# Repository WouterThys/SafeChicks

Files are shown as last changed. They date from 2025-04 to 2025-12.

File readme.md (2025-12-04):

# Safe Chicks

Chicks need to be safe so make door go brrrr.

## Ideas/Notes
 - Chord attacked to door and motor winds up/down to open/close door
 - Light sensor 
 - Limit switch -> use the iCab galenus switches? -> magnetic so will not weir out I guess
 - Solar powered?
 - Controller? What I have is:
    - Pico Pi
    - Arduino
    - Raspberry pi 3
    - Beaglebone black
    - Adafruit Huzzah -> has ESP.. 
 - Camera to see if checks are there -> would need raspberry for that (arduino is too lightweight)
 - DC motor
      https://www.farnell.com/datasheets/4376711.pdf?_gl=1*1atfsg3*_gcl_au*MjAyNTY1MDc1NS4xNzQxNjI0NTgy

## Used in V2

### Mouser
426-DRI0044
Fabrik. Artikelnum.: DRI0044
DFRobot 2x1.2A DC Motor Driv / Stroombeheer IC Ontwikkelinghulpmiddelen
TARIC:8473302000 ECCN:EAR99 COO:CN

426-FIT0489-D
Fabrik. Artikelnum.: FIT0489-D
DFRobot Turbo Metal Gear Wor / DFRobo-accessoires
TARIC:8471500090 ECCN:EAR99 COO:CN

653-D2HW-C223MR
Fabrik. Artikelnum.: D2HW-C223MR
Omron Electronics Subminiature Basic S / Basis- / klikschakelaars
TARIC:8536508099 ECCN:EAR99 COO:IT

### RobotShop
RB-Jsu-84 37mm Motor Mount For Titan Series (Pair) 5-4-G 1 1 0 €5.71 €5.71
RB-Sct-941 15T Timing Pinion Pulley (6mm) 02-6-B 1 1 0 €9.45 €9.45
RB-Phi-457 Waterproof Enclosure 200x120x75 w/ Transparent Lid M05-2-D 1 1 0 €13.12 €13.12

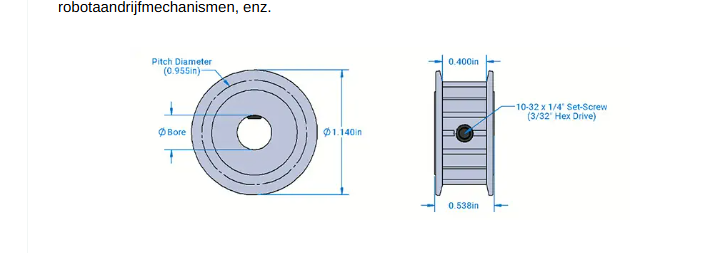
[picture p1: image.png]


## Usefull links
DIY chicken door:
https://davenaves.com/blog/interests-projects/chickens/chicken-coop/arduino-chicken-door/#

Battery management system
https://www.dfrobot.com/product-1714.html

Arduino low power
https://docs.arduino.cc/learn/electronics/low-power/

## Measurements

### POC Arduino Uno (17/03 16:20)
  - added 4[Ohm] resistor between 12V supply
  - Idle ~140mV => 4,9 mW
  - Run  ~1,30V => 423 mW

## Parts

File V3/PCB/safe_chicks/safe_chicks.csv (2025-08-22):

Reference | Value | Footprint | Datasheet | Qty | DNP | Exclude from BOM | Exclude from Board
C1,C2,C4,C10 | 100n | Capacitor_SMD:C_0603_1608Metric_Pad1.08x0.95mm_HandSolder | ~ | 4
C3 | 1u | Capacitor_Tantalum_SMD:CP_EIA-3216-10_Kemet-I_HandSolder | ~ | 1
C5 | 10u | Capacitor_Tantalum_SMD:CP_EIA-3216-10_Kemet-I_HandSolder | ~ | 1
C6,C7 | 10n | Capacitor_SMD:C_0603_1608Metric_Pad1.08x0.95mm_HandSolder | ~ | 2
C8,C9,C11,C12 | 1u | Capacitor_SMD:C_0603_1608Metric_Pad1.08x0.95mm_HandSolder | ~ | 4
D1 | 1007 | Diode_THT:D_DO-15_P10.16mm_Horizontal | ~ | 1
D2,D3,D4,D5,D6,D7 | LED_Small | LED_SMD:LED_0603_1608Metric_Pad1.05x0.95mm_HandSolder | ~ | 6
H1,H2,H3,H4 | MountingHole | MountingHole:MountingHole_3.2mm_M3_Pad_Via | ~ | 4 |  | Excluded from BOM
J1 | 5V | TerminalBlock:TerminalBlock_bornier-2_P5.08mm | ~ | 1
J2 | PGM | Connector_PinHeader_2.54mm:PinHeader_1x06_P2.54mm_Vertical | ~ | 1
J3 | Serial | Connector_Molex:Molex_PicoBlade_53047-0410_1x04_P1.25mm_Vertical | ~ | 1
J4 | Buttons | Connector_Molex:Molex_PicoBlade_53047-0410_1x04_P1.25mm_Vertical | ~ | 1
J5 | MTR | Connector_PinHeader_2.54mm:PinHeader_1x06_P2.54mm_Vertical | ~ | 1
J6 | Sensors | Connector_Molex:Molex_PicoBlade_53047-0410_1x04_P1.25mm_Vertical | ~ | 1
J8 | Switches | Connector_Molex:Molex_PicoBlade_53047-0410_1x04_P1.25mm_Vertical | ~ | 1
J9 | LED-Enable | Connector_PinHeader_2.54mm:PinHeader_1x03_P2.54mm_Vertical | ~ | 1
R1,R10,R11,R18,R20 | 10k | Resistor_SMD:R_0603_1608Metric_Pad0.98x0.95mm_HandSolder | ~ | 5
R2,R3 | 613k | Resistor_SMD:R_0603_1608Metric_Pad0.98x0.95mm_HandSolder | ~ | 2
R4 | 332k | Resistor_SMD:R_0603_1608Metric_Pad0.98x0.95mm_HandSolder | ~ | 1
R6,R7,R17,R19 | 100k | Resistor_SMD:R_0603_1608Metric_Pad0.98x0.95mm_HandSolder | ~ | 4
R8,R9,R12,R13,R14,R15 | 1k | Resistor_SMD:R_0603_1608Metric_Pad0.98x0.95mm_HandSolder | ~ | 6
R16 | 47k | Resistor_SMD:R_0603_1608Metric_Pad0.98x0.95mm_HandSolder | ~ | 1
SW1 | Reset | Button_Switch_THT:SW_PUSH_6mm_H4.3mm | ~ | 1
U1 | PIC18F2550-ISP | Package_DIP:DIP-28_W7.62mm | http://ww1.microchip.com/downloads/en/devicedoc/39632c.pdf | 1
Y1 | 16MHz | Crystal:Crystal_HC49-U_Vertical | ~ | 1

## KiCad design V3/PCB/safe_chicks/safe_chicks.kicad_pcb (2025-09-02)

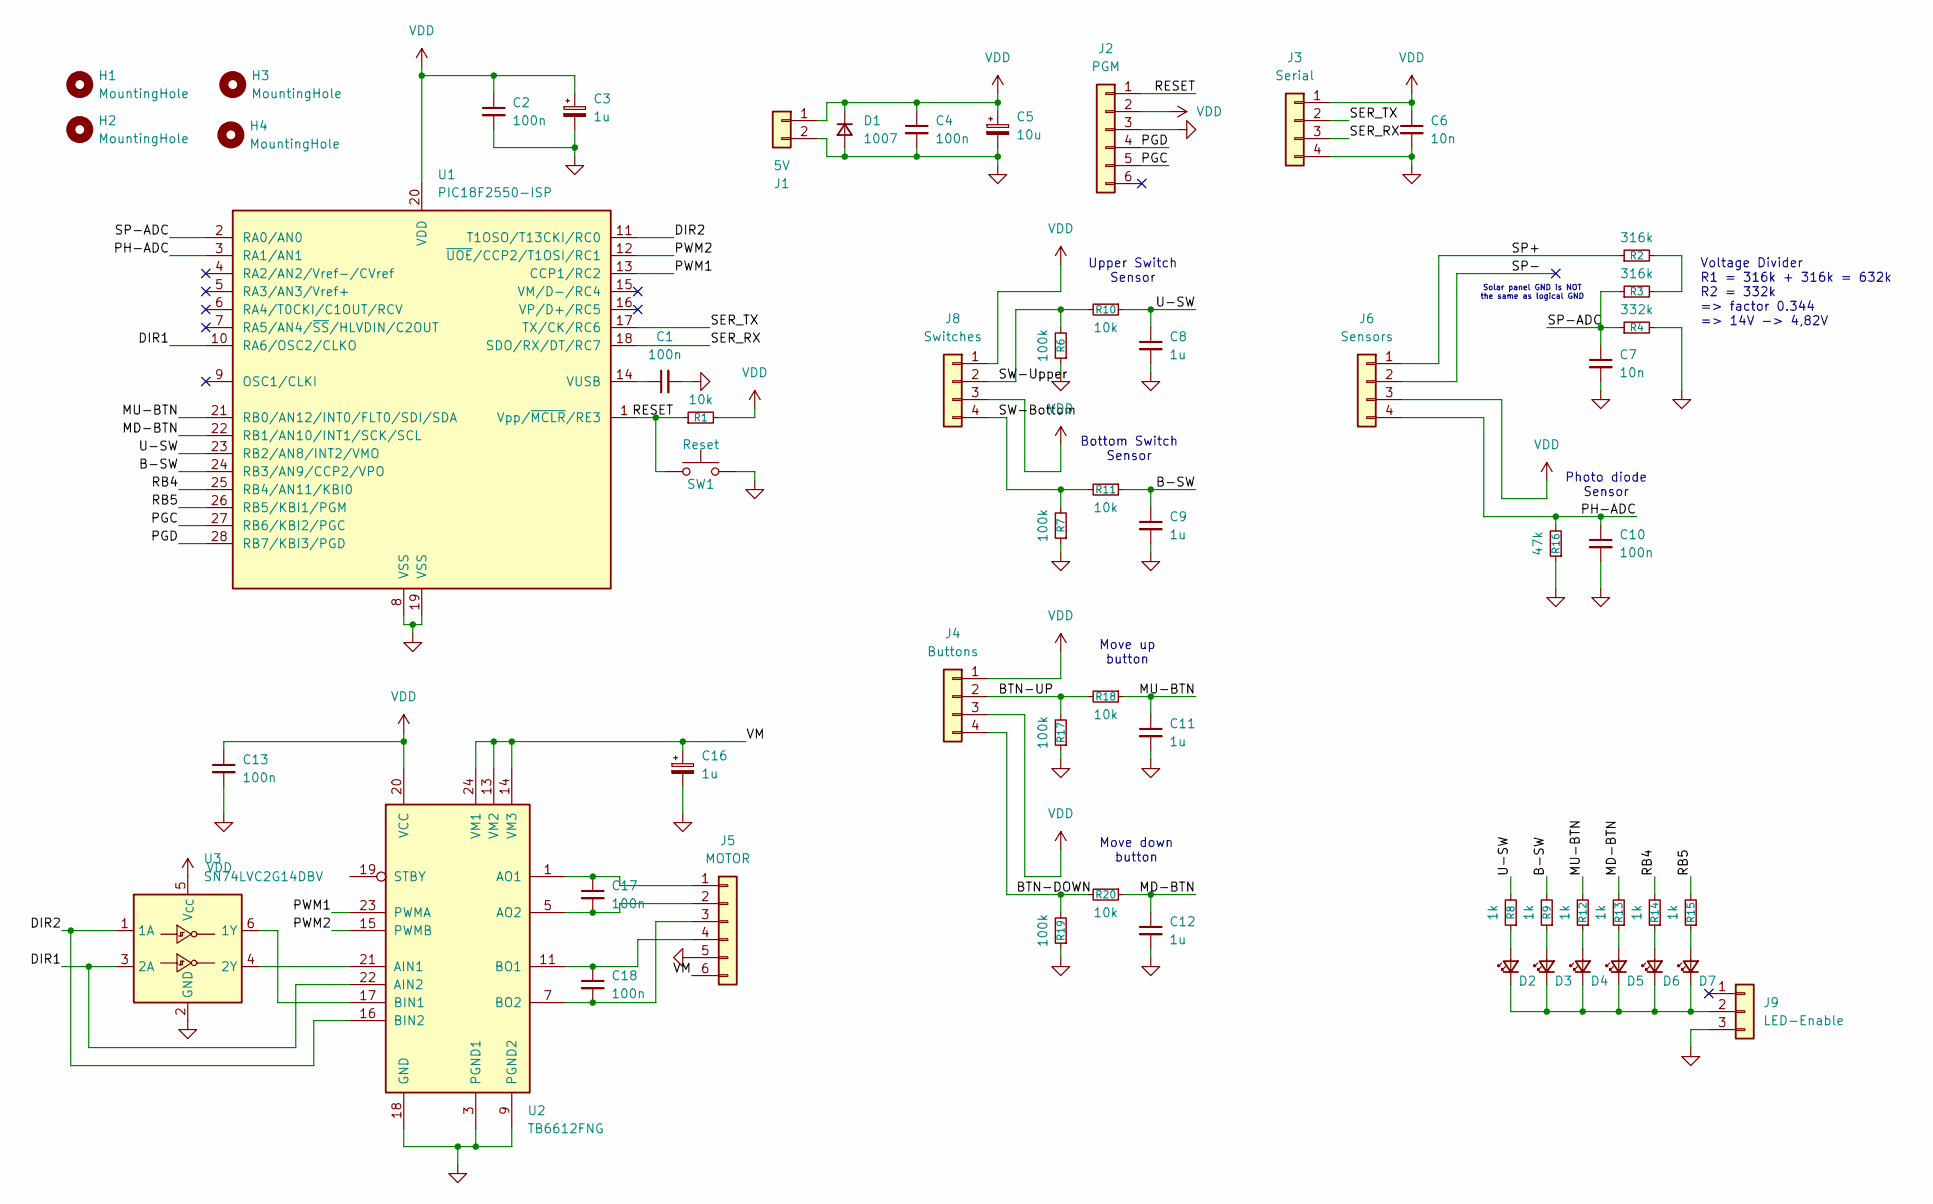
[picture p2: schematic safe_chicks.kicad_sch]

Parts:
C1, C2, C4, C10, C13, C17, C18: 100n; C_0603_1608Metric_Pad1.08x0.95mm_HandSolder
C3, C16: 1u; CP_EIA-3216-10_Kemet-I_HandSolder
C5: 10u; CP_EIA-3216-10_Kemet-I_HandSolder
C6, C7: 10n; C_0603_1608Metric_Pad1.08x0.95mm_HandSolder
C8, C9, C11, C12: 1u; C_0603_1608Metric_Pad1.08x0.95mm_HandSolder
D1: 1007; D_DO-15_P10.16mm_Horizontal
D2, D3, D4, D5, D6, D7: LED_Small; LED_0603_1608Metric_Pad1.05x0.95mm_HandSolder
H1, H2, H3, H4: MountingHole; MountingHole_3.2mm_M3_Pad_Via
J1: 5V; TerminalBlock_bornier-2_P5.08mm
J2: PGM; PinHeader_1x06_P2.54mm_Vertical
J3: Serial; Molex_PicoBlade_53047-0410_1x04_P1.25mm_Vertical
J4: Buttons; Molex_PicoBlade_53047-0410_1x04_P1.25mm_Vertical
J5: MOTOR; PinHeader_1x06_P2.54mm_Vertical
J6: Sensors; Molex_PicoBlade_53047-0410_1x04_P1.25mm_Vertical
J8: Switches; Molex_PicoBlade_53047-0410_1x04_P1.25mm_Vertical
J9: LED-Enable; PinHeader_1x03_P2.54mm_Vertical
R1, R10, R11, R18, R20: 10k; R_0603_1608Metric_Pad0.98x0.95mm_HandSolder
R2, R3: 316k; R_0603_1608Metric_Pad0.98x0.95mm_HandSolder
R4: 332k; R_0603_1608Metric_Pad0.98x0.95mm_HandSolder
R6, R7, R17, R19: 100k; R_0603_1608Metric_Pad0.98x0.95mm_HandSolder
R8, R9, R12, R13, R14, R15: 1k; R_0603_1608Metric_Pad0.98x0.95mm_HandSolder
R16: 47k; R_0603_1608Metric_Pad0.98x0.95mm_HandSolder
SW1: Reset; SW_PUSH_6mm_H4.3mm
U1: PIC18F2550-ISP; DIP-28_W7.62mm
U2: TB6612FNG; SSOP-24_5.3x8.2mm_P0.65mm
U3: SN74LVC2G14DBV; SOT-23-6

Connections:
/B-SW: C9.1, R9.2, R11.1, U1.24 (RB3/AN9/CCP2/VPO)
/BTN-DOWN: J4.4, R19.2, R20.2
/BTN-UP: J4.2, R17.2, R18.2
/DIR1: U1.10 (RA6/OSC2/CLKO), U2.22 (AIN2), U3.3 (2A)
/DIR2: U1.11 (T1OSO/T13CKI/RC0), U2.16 (BIN2), U3.1 (1A)
/MD-BTN: C12.1, R13.2, R20.1, U1.22 (RB1/AN10/INT1/SCK/SCL)
/MU-BTN: C11.1, R12.2, R18.1, U1.21 (RB0/AN12/INT0/FLT0/SDI/SDA)
/PGC: J2.5, U1.27 (RB6/KBI2/PGC)
/PGD: J2.4, U1.28 (RB7/KBI3/PGD)
/PH-ADC: C10.1, J6.4, R16.2, U1.3 (RA1/AN1)
/PWM1: U1.13 (CCP1/RC2), U2.23 (PWMA)
/PWM2: U1.12 (~UOE/CCP2/T1OSI/RC1), U2.15 (PWMB)
/RB4: R14.2, U1.25 (RB4/AN11/KBI0)
/RB5: R15.2, U1.26 (RB5/KBI1/PGM)
/RESET: J2.1, R1.1, SW1.1, U1.1 (Vpp/~MCLR/RE3)
/SER_RX: J3.3, U1.18 (SDO/RX/DT/RC7)
/SER_TX: J3.2, U1.17 (TX/CK/RC6)
/SP+: J6.1, R2.1
/SP-: J6.2
/SP-ADC: C7.1, R3.1, R4.1, U1.2 (RA0/AN0)
/SW-Bottom: J8.4, R7.2, R11.2
/SW-Upper: J8.2, R6.2, R10.2
/U-SW: C8.1, R8.2, R10.1, U1.23 (RB2/AN8/INT2/VMO)
/VM: C16.1, J5.6, U2.13 (VM2), U2.14 (VM3), U2.24 (VM1)
GND: C1.2, C2.2, C3.2, C4.2, C5.2, C6.2, C7.2, C8.2, C9.2, C10.2, C11.2, C12.2, C13.2, C16.2, D1.2 (A), J1.2, J2.3, J3.4, J5.5, J9.3, R4.2, R6.1, R7.1, R16.1, R17.1, R19.1, SW1.2, U1.8 (VSS), U1.19 (VSS), U2.3 (PGND1), U2.4 (PGND1), U2.9 (PGND2), U2.10 (PGND2), U2.18 (GND), U3.2 (GND)
unnamed: D2.2 (A), R8.1
unnamed: D2.1 (K), D3.1 (K), D4.1 (K), D5.1 (K), D6.1 (K), D7.1 (K), J9.2
unnamed: D3.2 (A), R9.1
unnamed: D4.2 (A), R12.1
unnamed: D5.2 (A), R13.1
unnamed: D6.2 (A), R14.1
unnamed: D7.2 (A), R15.1
unnamed: C17.1, J5.1, U2.1 (AO1), U2.2 (AO1)
unnamed: C17.2, J5.2, U2.5 (AO2), U2.6 (AO2)
unnamed: C18.2, J5.3, U2.7 (BO2), U2.8 (BO2)
unnamed: C18.1, J5.4, U2.11 (BO1), U2.12 (BO1)
unnamed: R2.2, R3.2
unnamed: C1.1, U1.14 (VUSB)
unnamed: U2.21 (AIN1), U3.4 (2Y)
unnamed: U2.17 (BIN1), U3.6 (1Y)
VDD: C2.1, C3.1, C4.1, C5.1, C6.1, C13.1, D1.1 (K), J1.1, J2.2, J3.1, J4.1, J4.3, J6.3, J8.1, J8.3, R1.2, U1.20 (VDD), U2.20 (VCC), U3.5 (V_{CC})

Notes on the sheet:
Move down button
Solar panel GND is NOT the same as logical GND
Bottom Switch Sensor
Move up button
Photo diode Sensor
Upper Switch Sensor
Voltage Divider R1 = 316k + 316k = 632k R2 = 332k => factor 0.344 => 14V -> 4,82V

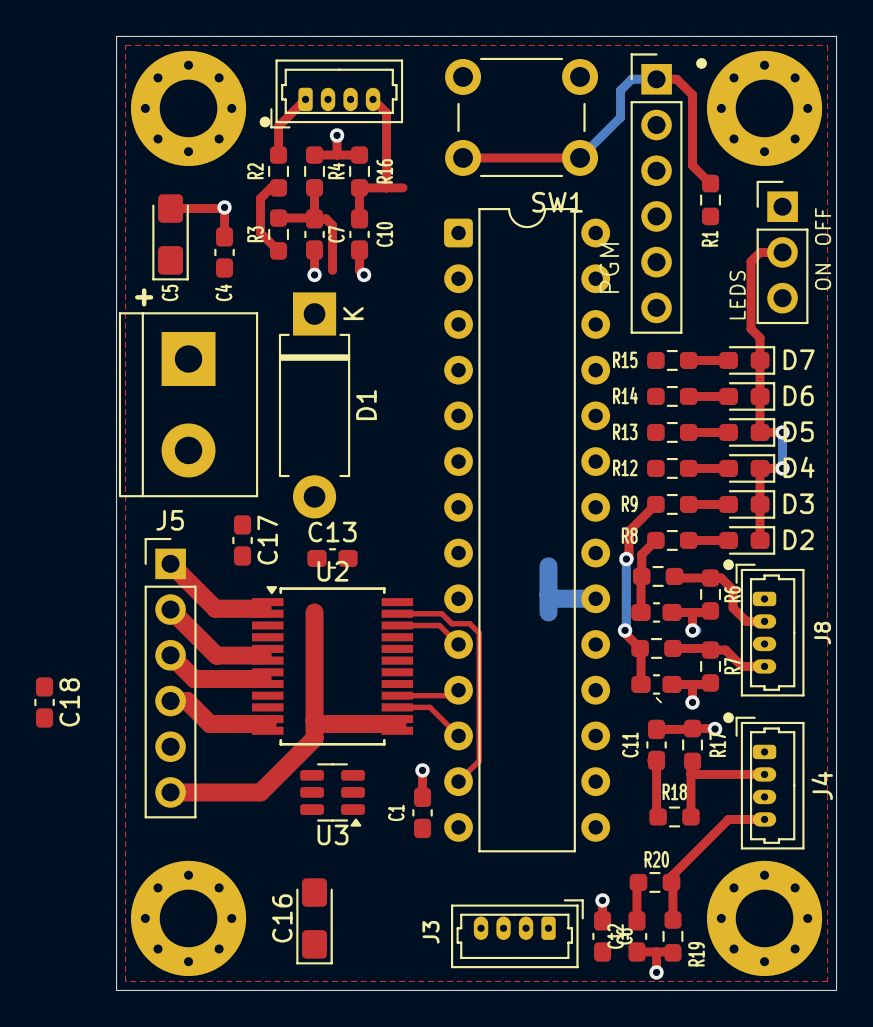
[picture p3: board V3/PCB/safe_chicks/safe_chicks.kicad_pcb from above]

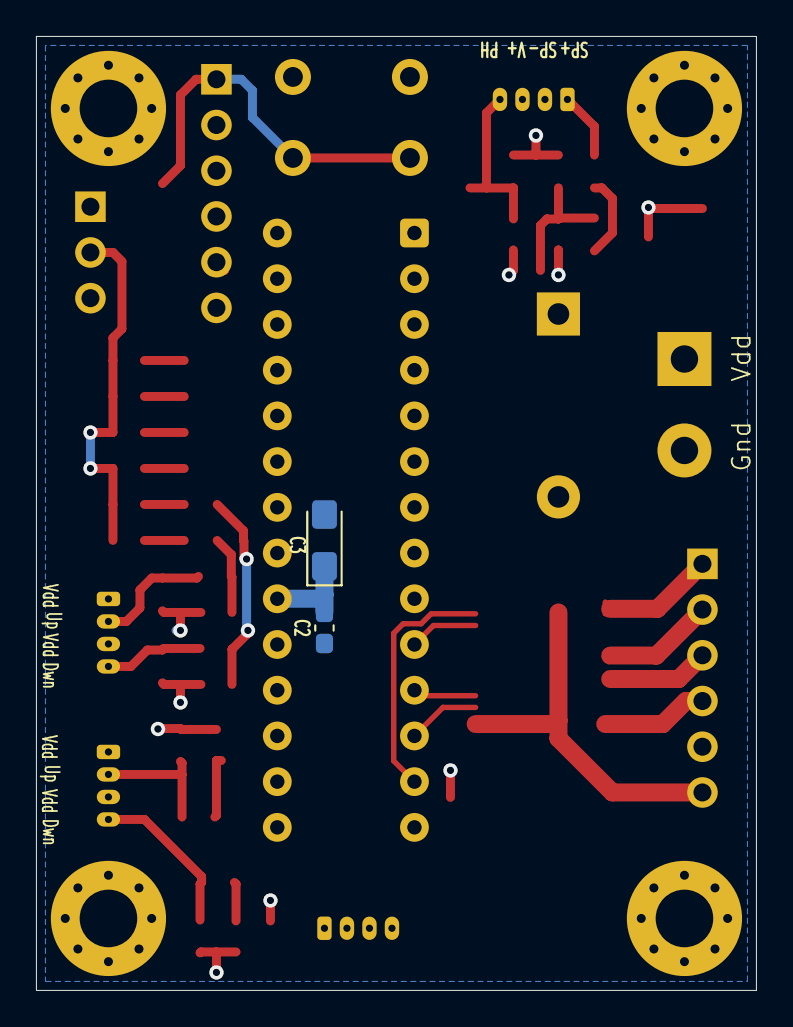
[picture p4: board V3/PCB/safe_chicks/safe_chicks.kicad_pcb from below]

Board: 2 copper layers, 40.0 x 53.0 mm, 58 parts (2 on the bottom side), 40 nets.

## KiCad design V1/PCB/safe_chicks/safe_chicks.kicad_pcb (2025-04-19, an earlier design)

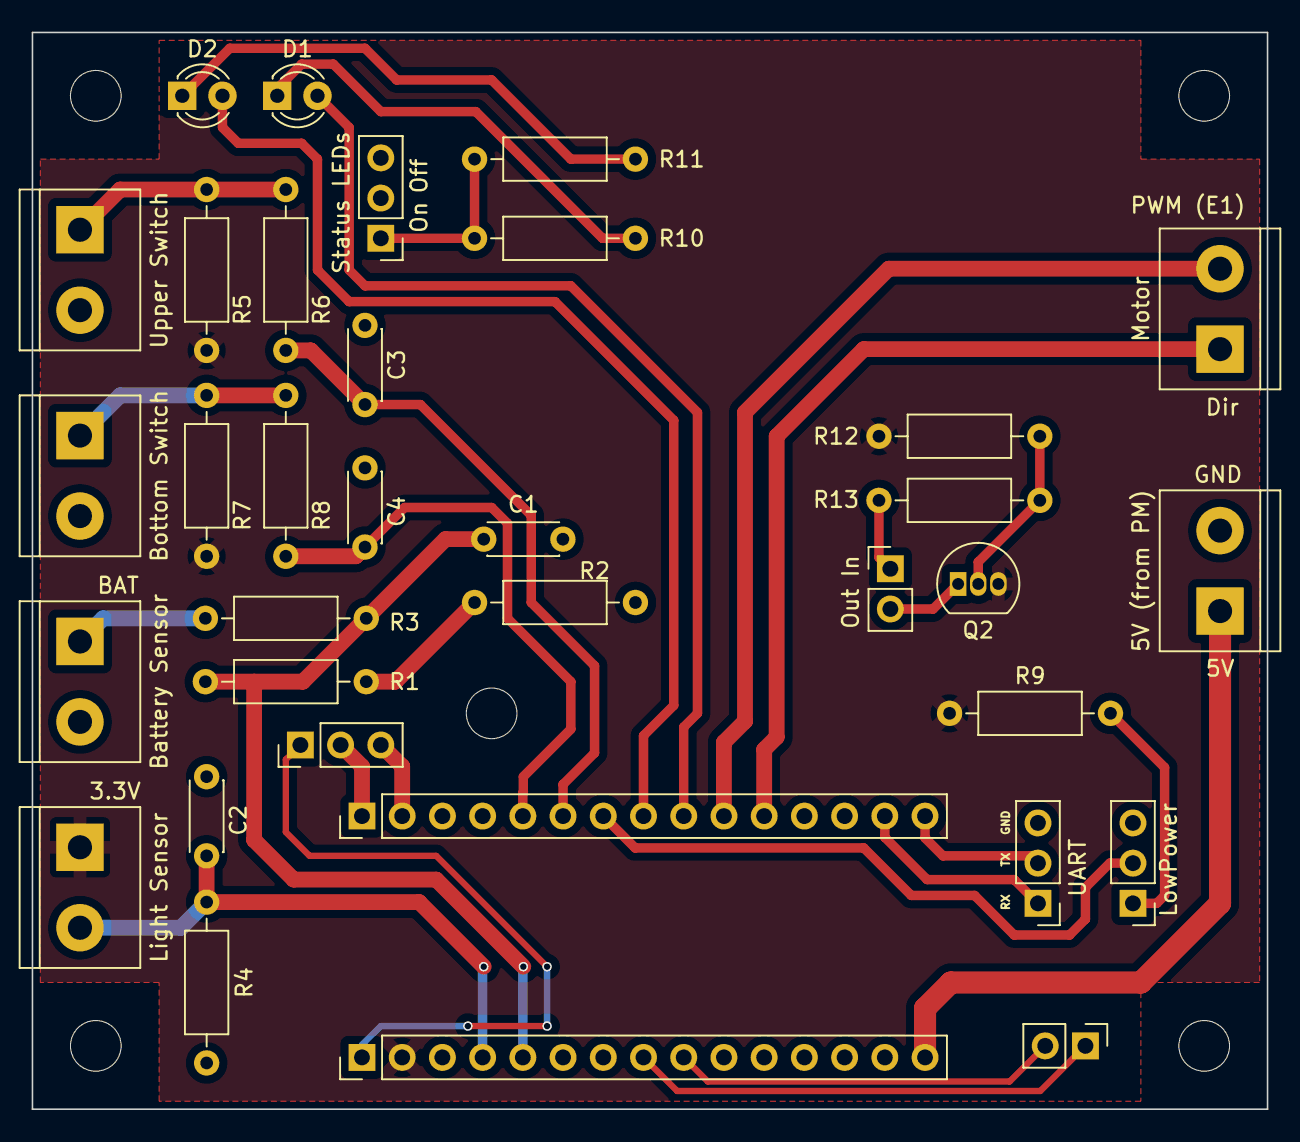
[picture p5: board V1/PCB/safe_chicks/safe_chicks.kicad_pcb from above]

Board: 2 copper layers, 78.0 x 68.0 mm, 39 parts (0 on the bottom side), 30 nets.

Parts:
C1, C2: 100n; C_Disc_D4.3mm_W1.9mm_P5.00mm
C3, C4: 1u; C_Disc_D4.3mm_W1.9mm_P5.00mm
D1, D2: LED; LED_D3.0mm
H1, H2, H3, H4, H5: MountingHole; MountingHole_3.2mm_M3
J1, J2: Conn_01x15; PinHeader_1x15_P2.54mm_Vertical
J3: Battery Sensor; TerminalBlock_bornier-2_P5.08mm
J4: Light Sensor; TerminalBlock_bornier-2_P5.08mm
J5: Upper Switch; TerminalBlock_bornier-2_P5.08mm
J6: Bottom Switch; TerminalBlock_bornier-2_P5.08mm
J7: Motor; TerminalBlock_bornier-2_P5.08mm
J8: 5V (from PM); TerminalBlock_bornier-2_P5.08mm
J9: LowPower; PinHeader_1x03_P2.54mm_Vertical
J10: Status LEDs; PinHeader_1x03_P2.54mm_Vertical
J11: UART; PinHeader_1x03_P2.54mm_Vertical
J12: SPI; PinHeader_1x03_P2.54mm_Vertical
J13, J14: Conn_01x02; PinHeader_1x02_P2.54mm_Vertical
Q2: BS250; TO-92_Inline
R1, R2, R3: 1M; R_Axial_DIN0207_L6.3mm_D2.5mm_P10.16mm_Horizontal
R4: 47k; R_Axial_DIN0207_L6.3mm_D2.5mm_P10.16mm_Horizontal
R5, R6, R7, R8, R9: 100k; R_Axial_DIN0207_L6.3mm_D2.5mm_P10.16mm_Horizontal
R10, R11: 220; R_Axial_DIN0207_L6.3mm_D2.5mm_P10.16mm_Horizontal
R12: 10k; R_Axial_DIN0207_L6.3mm_D2.5mm_P10.16mm_Horizontal
R13: 1k; R_Axial_DIN0207_L6.3mm_D2.5mm_P10.16mm_Horizontal

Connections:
+3V3: J1.2, J4.1, Q2.3 (S), R5.1, R7.1, R9.1, R12.1
/*D3: J2.10, J7.2
/*D5: D2.2 (A), J2.8
/*D6: J2.7, J9.2
/*D11/MOSI: J2.2, J12.3
/A0: C2.1, J1.4, J4.2, R4.1
/A1: C1.1, J1.5, R1.1, R3.2
/A4/SDA: J1.8, J13.1
/A5/SCL: J1.9, J13.2
/D0/RX: J2.14, J11.1
/D1/TX: J2.15, J11.2
/D2: J2.11, J7.1
/D4: D1.2 (A), J2.9
/D7: C3.1, J2.6, R6.2
/D8: C4.1, J2.5, R8.2
/D12/MISO: J2.1, J12.2
/D13/SCK: J1.1, J12.1
GND: C1.2, C2.2, C3.2, C4.2, J1.14, J2.12, J3.2, J5.2, J6.2, J8.2, J9.3, J10.2, J11.3, R2.2, R4.2
unnamed: D1.1 (K), R10.1
unnamed: D2.1 (K), R11.1
unnamed: J3.1, R3.1
unnamed: J5.1, R5.2, R6.1
unnamed: J6.1, R7.2, R8.1
unnamed: J9.1, R9.2
unnamed: J10.1, R10.2, R11.2
unnamed: J14.1, R13.1
unnamed: J14.2, Q2.1 (D)
unnamed: Q2.2 (G), R12.2, R13.2
unnamed: R1.2, R2.1
VCC: J1.15, J8.1

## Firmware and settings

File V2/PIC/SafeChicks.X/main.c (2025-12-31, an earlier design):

#include <builtins.h>
#include <stdbool.h>
#include <xc.h>

#include "config.h"

#include "Controllers/FSM_Controller.h"
#include "Drivers/ADC_Driver.h"
#include "Drivers/MOTOR_Driver.h"
#include "Drivers/TMR0_Driver.h"
#include "Drivers/UART_Driver.h"

#if DEBUG_MODE
#include <stdio.h>
#endif


/*******************************************************************************
 *                      Local defines
 ******************************************************************************/

/*******************************************************************************
 *                      Function and type definitions
 ******************************************************************************/

/**
 * Main initialisation function.
 * Note that this will only be called only after a reset.
 *
 * Will enable all timers and interrupts for other peripherals to work.
 * Enables the FSM, Motor, ... code
 */
static void initialize(void);

/**
 * Enters the MCU in sleep mode.
 * This will update the Timer0 values to go for a long sleep
 */
static void goToSleep(void);

/*******************************************************************************
 *                      Variables
 ******************************************************************************/
bool test = false;
volatile bool runFSM = false;

#if DEBUG_MODE
#define DEBUG_BUFFER_SIZE 100
char debugBuffer[DEBUG_BUFFER_SIZE];

uint8_t debugCounter = 0;
static void buildConfigString(char *dst, uint8_t size);

#endif

/*******************************************************************************
 *                      Function implementation
 ******************************************************************************/

void initialize(void) {
  /* Oscillators setup */
  OSCCONbits.IRCF = 0b100; /* 1MHz */
  OSCCONbits.SCS = 0b10;   /* Internal oscillator, RC_RUN power mode */
  while (OSCCONbits.IOFS == 0)
    ; /* Wait for OSC to be stable */

  /* Port setup */
  TRISA = 0x00;
  TRISB = 0x00;
  TRISC = 0x00;

  PORTA = 0x00;
  PORTB = 0x00;
  PORTC = 0x00;

  /* Interrupt setup */
  INTCON2bits.INTEDG0 = 1; /* Interrupt on rising edge               */
  //INTCONbits.INT0IP = 0;  /* Low priority                           */
  INTCONbits.INT0IF = 0;  /* Clear flag                             */
  INTCONbits.INT0IE = 1;  /* Enables the INT0 external interrupt    */
  
  INTCON2bits.INTEDG1 = 1; /* Interrupt on rising edge               */
  INTCON3bits.INT1IP = 1;  /* Low priority                           */
  INTCON3bits.INT1IF = 0;  /* Clear flag                             */
  INTCON3bits.INT1IE = 1;  /* Enables the INT0 external interrupt    */

  RCONbits.IPEN = 1;   /* Enable priority levels on interrupts   */
  INTCONbits.PEIE = 1; /* Enable all peripheral interrupts       */

  /* My own code setups */
  D_TMR0_Init(TIMER_MODE_WORK);
  D_MOTOR_Init();
  D_UART_Init();
  D_ADC_Init();
  C_FSM_Init(goToSleep);

  /* Enable stuff */
  D_TMR0_Enable(true);
  D_UART_Enable(true);
  INTCONbits.GIEH = 1; /* Enables all high-priority interrupts   */
  INTCONbits.GIEL = 1; /* Enable low interrupts                  */

  D_UART_Write("start\n");
}

void goToSleep(void) {

#if DEBUG_MODE

  /* Print the current configuration every 10 sleeps */
  if (debugCounter % 10 == 0) {
    buildConfigString(debugBuffer, DEBUG_BUFFER_SIZE);
    D_UART_Write(debugBuffer);
    debugCounter = 0;
  }

  /* Debug FSM state */
  C_FSM_ToString(debugBuffer, DEBUG_BUFFER_SIZE);
  D_UART_Write(debugBuffer);

  debugCounter++;

#endif

  /**
   * We will need peripheral clock so go to RC_IDLE mode on SLEEP
   */

  OSCCONbits.IDLEN = 1; /* Idle mode on SLEEP instruction         */

  D_TMR0_Init(TIMER_MODE_SLEEP);
  D_TMR0_Enable(true);
  /* Lets go! */
  SLEEP();

  /* Wake up again */
  D_TMR0_Init(TIMER_MODE_WORK);
  D_TMR0_Enable(true);
}

#if DEBUG_MODE
void buildConfigString(char *dst, uint8_t size) {

    snprintf(dst, size,
        "C:%" PRIu8 ",%" PRIu8 ",%" PRIu8 ",%" PRIu8 ",%" PRIu8 ",%" PRIu8 ",%" PRIu16 ",%" PRIu16 ",%" PRIu16 "\r\n", 
        DAY_THRESHOLD,
        NIGHT_THRESHOLD,
        SLEEP_COUNT,
        DAY_COUNT,
        MOTOR_FULL_SPEED,
        MOTOR_HALF_SPEED,
        MAX_MOTOR_COUNT,
        MOTOR_DOWN_FULL_CNT,
        MOTOR_DOWN_SLOW_CNT
);

}
#endif

int main(void) {

  __delay_ms(100);
  initialize();
  __delay_ms(100);

  while (1) {
    if (runFSM) {
      runFSM = false;
      C_FSM_Tick();
    }
  }

  return 0;
}

void __interrupt(low_priority) _LowInterruptManager(void) {
  /* Check if TMR0 interrupt is enabled and if the interrupt flag is set */
  if (INTCONbits.TMR0IE == 1 && INTCONbits.TMR0IF == 1) {
    runFSM = true;
    INTCONbits.TMR0IF = 0; /* clear the TMR0 interrupt flag */
  }
}

void __interrupt(high_priority) _HighInterruptManager(void) {

  /* Check if INT0 interrupt is enabled and if the interrupt flag is set */
  if (INTCONbits.INT0IE == 1 && INTCONbits.INT0IF == 1) {
    runFSM = true;
    INTCONbits.INT0IF = 0; /* clear the INT2 interrupt flag */
  }
  
   /* Check if INT1 interrupt is enabled and if the interrupt flag is set */
  if (INTCON3bits.INT1IE == 1 && INTCON3bits.INT1IF == 1) {
    runFSM = true;
    INTCON3bits.INT1IF = 0; /* clear the INT2 interrupt flag */
  }

}

/* THE END */

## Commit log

2025-03-17 Some first setup
    [timing.xlsx]
2025-03-17 Motor dimensions
2025-03-31 Add first PCB
    [safe_chicks.kicad_pcb, safe_chicks.kicad_sch]
2025-03-31 update pcb
    [safe_chicks.kicad_pcb]
2025-03-31 Created PCB
    [safe_chicks.kicad_pcb, safe_chicks.kicad_sch]
2025-04-19 add some test programs to finetune sensors and delays
2025-04-19 test motor
2025-04-20 faster motor start and stop
2025-04-20 motor delays
2025-05-29 Run the motor a little slower, only check low power pin iso debug flag
2025-06-14 Slow down motor a litte to 50%
2025-08-18 Make ready for V2
    [safe_chicks.kicad_pcb, safe_chicks.kicad_sch]
2025-08-19 Create V2 PCB and test solar panel
    [safe_chicks.kicad_pcb, safe_chicks.kicad_sch]
2025-08-22 More on PCB V2
    [safe_chicks.csv, safe_chicks.kicad_pcb, safe_chicks.kicad_sch]
2025-08-26 First try of the mplab project
    [safe_chicks.kicad_pcb]
2025-08-26 Internal OSC and T0 testing with interrupts WORKS
2025-08-26 First setup of the motor
2025-08-29 FSM is working with buttons and motor runs
    [safe_chicks.kicad_pcb, safe_chicks.kicad_sch]
2025-09-01 This works but sensors could be better
    [safe_chicks.kicad_sch]
2025-09-02 Some ideas on PCB V3
    [safe_chicks.csv, safe_chicks.kicad_pcb, safe_chicks.kicad_sch]
2025-09-02 Setting motor speeds to finetune
2025-09-02 Now with interrupts on the button up pin
2025-09-02 Move button pins so they can be used for interrupts
    [safe_chicks.kicad_pcb, safe_chicks.kicad_sch]
2025-09-04 print FSM state every time before going to sleep. Add script to analyse
2025-09-04 Cleaner debugging with sensors
2025-09-05 I think we are ready
    [safe_chicks.kicad_sch]
2025-11-29 Added parts to readme
    [safe_chicks.kicad_sch]
2025-12-31 Increase closing time and add night fake when both buttons are pushed
